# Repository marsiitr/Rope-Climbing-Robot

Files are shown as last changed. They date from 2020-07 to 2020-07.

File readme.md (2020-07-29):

<h1>Rope-Climbing-Robot</h1>
 <p align="justify">
Srishti 2020
</p>

## Abstract ##
<p align="justify">
This Rope climbing bot is used to climb ropes in an easy and efficient manner to reduce manual labour.Motorised rollers are used for climbing and a leadscrew is used for the gripping.
</p>
<p align="centre">
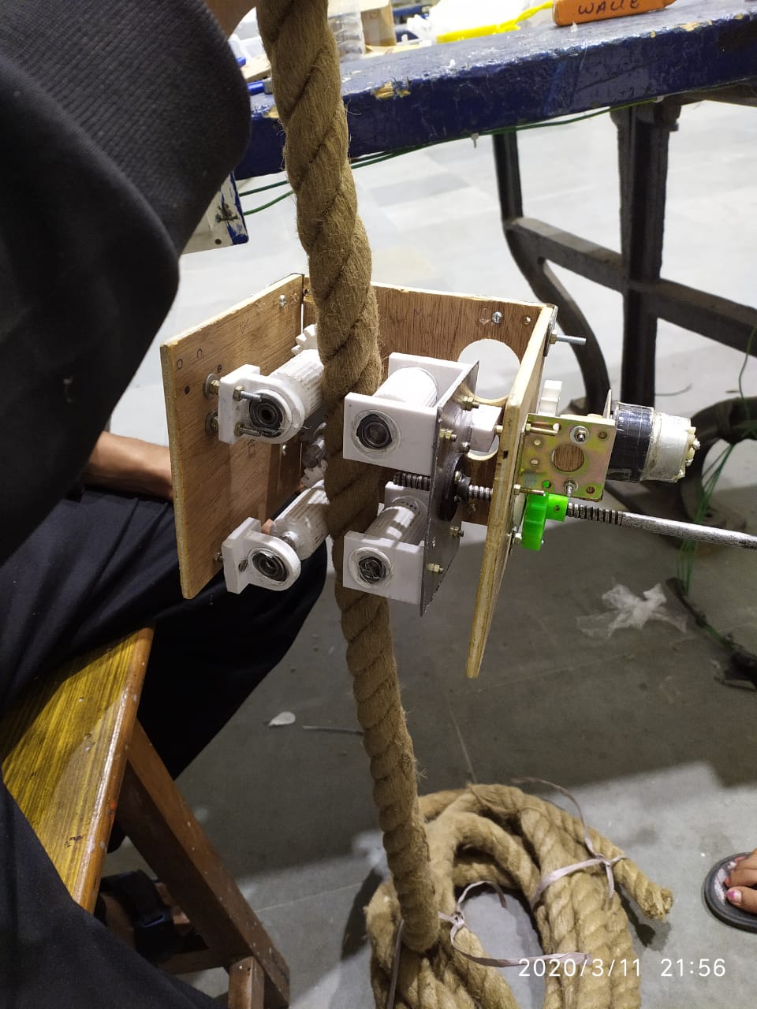
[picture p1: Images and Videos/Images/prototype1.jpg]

<!-- abstract-->
</p>

## Motivation ##
  <p align="justify">
People from various fields like mining , military , or other often come across situations where they can not get direct access to certain area say inside a cave in a mine .
There was a need of rope climbing robot which uses a single rope and can reach easily to any desired place in any terrain and most of the robots we come across uses double rope and are difficult to use. Also many day to day households work can be done easily with a rope climbing robot and thus we need a robot which can used in daily lives .     
</p>
<!-- motivation-->

## Mechanical aspect ##
<p align="justify">
In rope climbing robot two aspects are especially important grip on the rope and smoothness while movement . <br>
These two characteristics are important to carry a weight with a robot and easily maintain a overall stability of the robot . The design presented here for rope climmbing is a wheel based system since they are highly and easy to build.
</p>

#### Sliding roller ####
<p align="justify">
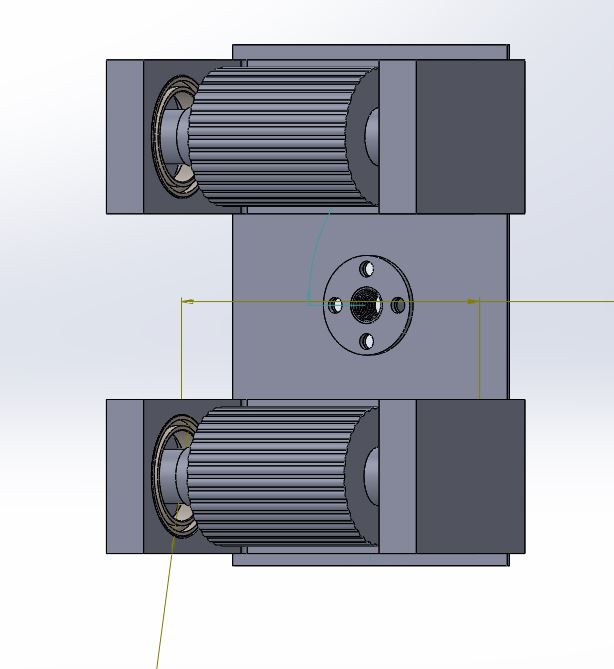
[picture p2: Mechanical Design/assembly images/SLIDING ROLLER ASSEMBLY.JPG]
<br>
This is a common and serves in both gripping mechanism and climbing mechanism . The assembly consists of two wheels attached to a rectangular metal sheet which is attached to the lead screw nut .<br>
The wheels are connected to the sheet with 3-D printed supports , bearings and shafts such that they are free to rotate about the shaft .
</p>

#### Encoder motor assembly ####
<p align="justify">
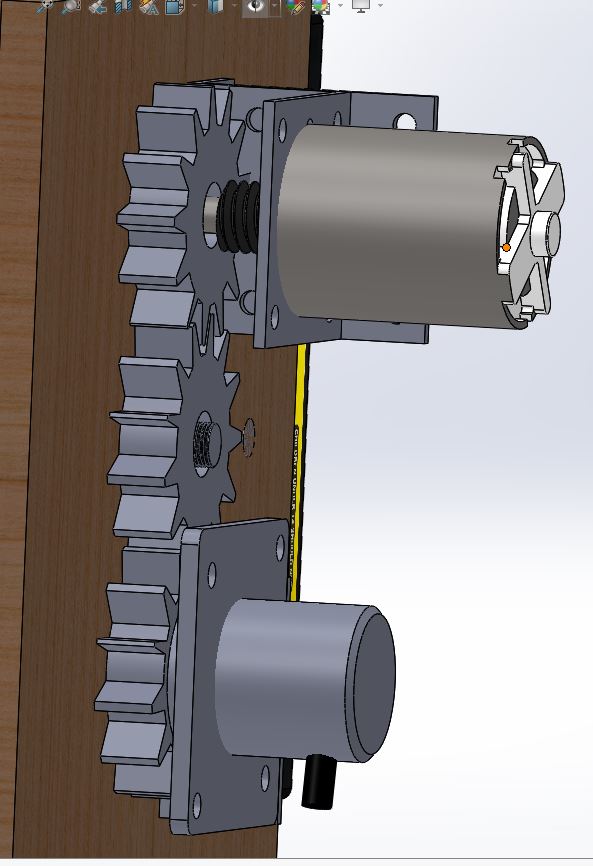
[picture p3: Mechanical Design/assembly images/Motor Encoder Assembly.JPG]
<br>
To grip the rope , sliding roller assembly has  to ascend on a lead screw , for that a spur gear is attached to the lead screw on the rear side . An encoder and motor are also attached sideways such that the lead screw attached to the spur gear simultaneously runs the spur gear attached to the encoder and the motor. <br>
For the working of the assembly , when the motor rotates , the spur gear rotates the lead screw which in turn rotates the encoder shaft through the trail of gears . The information of number of the rotations which the motor has to perform is already calculated and fitted into the encoder . Thus we can grip the rope.
</p>

#### Slider assembly ####
<p align="justify">
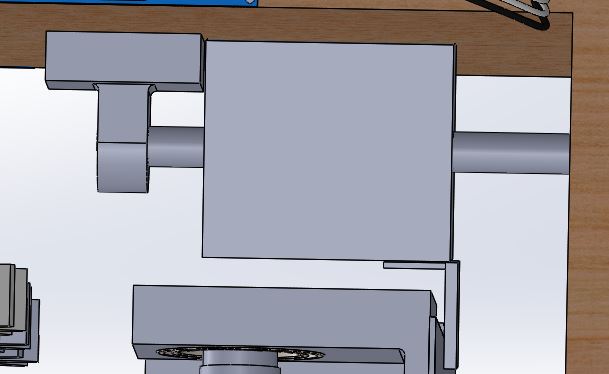
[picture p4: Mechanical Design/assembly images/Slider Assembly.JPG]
<br>
To prevent the sliding roller assembly to deviate from its path in a rotatory motion it is supported with a slider assembly. The slider is created with a shaft and a rectangular box which can slide on it . It is connected to "SRE" by a L hinge. <br>
The slider also creates a second support for the lead screw . Otherwise the lead screw will deviate from its position.
</p>

#### Motor wheel assembly ####
<p align="justify">
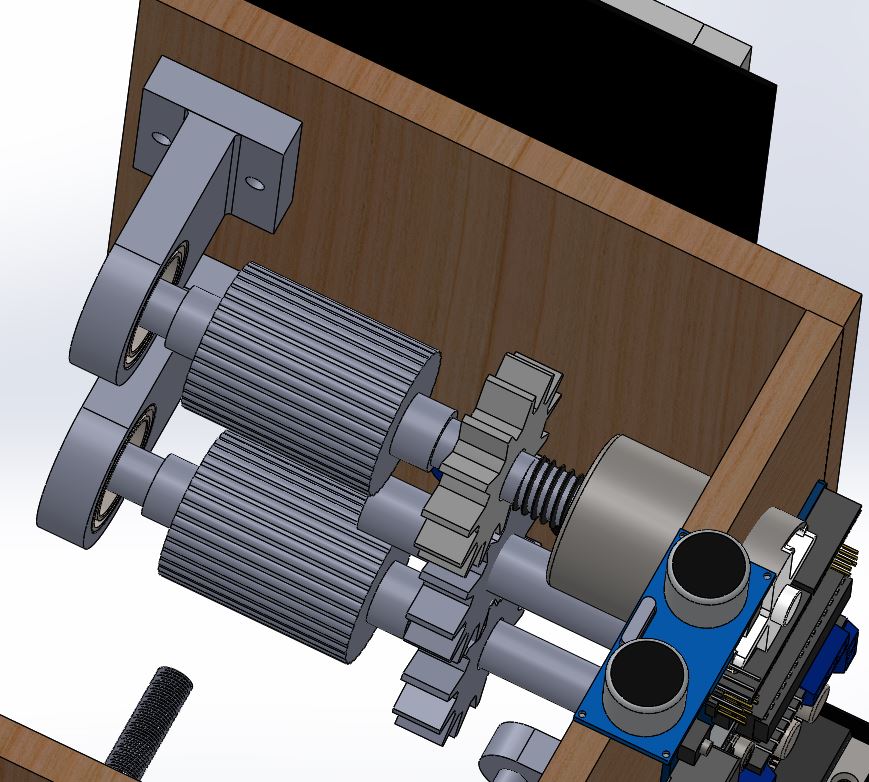
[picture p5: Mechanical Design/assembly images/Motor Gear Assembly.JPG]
<br>
After gripping the rope firmly, the bot has to climb the rope . The basic principal used along the rope is rolling. <br>
The design consists of a DC motor which is connected to three spur gear asssembly . The end gears are connected to each wheel . The design consists of two wheel pairs on either side of the rope. <br>
The wheels rolls on the surface of the rope which is powered by a DC motor (motor should provide high torque and power). In presence of sufficient friction between the wheels and the rope , the robot traverses the rope . The wheel should offer sufficient friction to support the robot in the vertical position . <br>
The other way to arrange the wheels is in a zig-zag pattern which increases the area of contact which in turn increases the friction.<br>
Let the radius of the wheel be r and θ is the angle of contact and h is the rope thickness. The surface area S in contact with the wheel is given as <br>
 <blockquote>S = (2πrhθ)/360</blockquote>
</p>

## Electronic aspect ##

- Electronic Components used
  
 1. Arduino Uno
 2. dc motors
 3. Ultrasonic distance sensors
 4. Encoder
 5. L298n motor controller
 6. Battery
 7. Connecting wires and jumpers
 
- Total two dc motors were used. One to grab the rope with the help of an encoder and the second for climbing the rope.</li>
- Two ultrasonic distance sensors were used to measure the distance of the bot from the floor and the top end of the rope.</li>
- dc motors were powered through Li-Po 12V dc battery.</li>

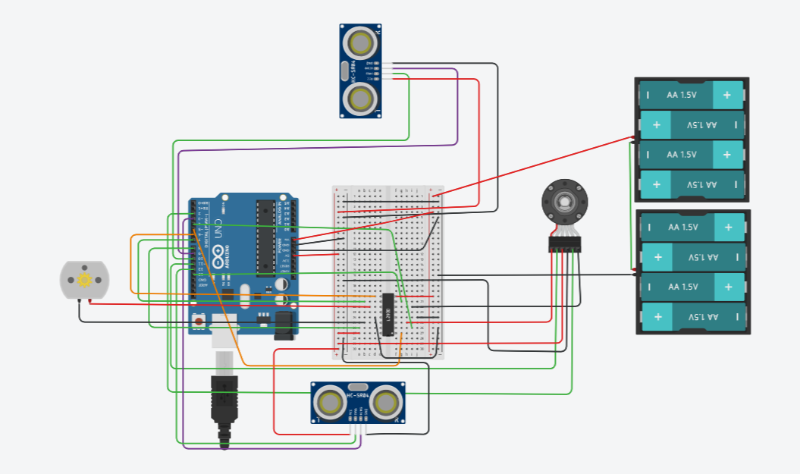
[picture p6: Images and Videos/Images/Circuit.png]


## Workflow ##

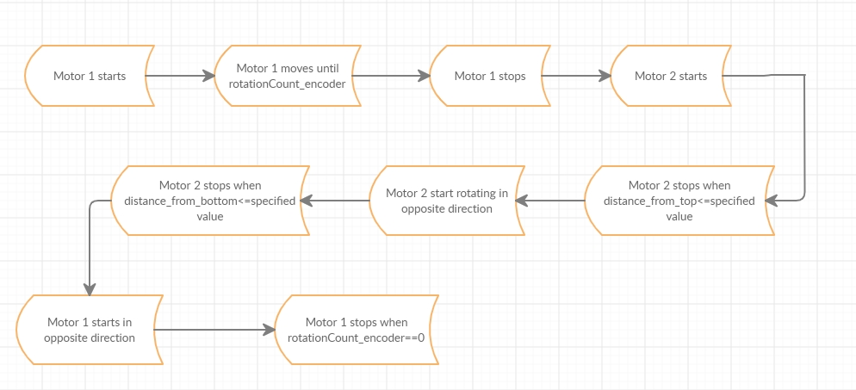
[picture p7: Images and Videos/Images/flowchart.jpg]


## Cost structure ##

<!-- cost structure-->

| materials|quantity|cost|
|:-----|:-----|:-----|
|Arduino UNO|1|425|
|Lipo battery|1|1100|
|Motor controller|1|160|
|Ultrasonic sensor|2|360|
|DC motor|2|300|
|Lead screw|1|600|
|Materials for body|1|1230|
|Manufacturing|1|600|
|*total*||4775|

## Applications ##

<p align="justify">
Robot is planned to serve the following tasks:
</p>

- It can be used to carry weights or to drop weights from some height.

- When equipped with camera, the robot can be used for surveillence.

- When equipped with cleaners, it can be used to clean glasses of windows or walls.

- Robot can be used to take pictures or to make videos from different heights.

<!-- apllications-->
## Limitations ##

1. The bot cannot climb horizontal ropes or ropes at some Angles.

2. The bot cannot traverse rope having some obstacles like knots or bend.

## Future improvements ##

1. The load carrying capacity can be improved by using stronger motors and parts.
2. Image detection software can be incorporated with the help of a camera , so that it can detect a rope on its own and climb it.
3. Modification in the design can be made so that it can measure its diameter of the rope without prefeding the data into the encoder.
4. Pneaumatics can be introduced in the the model to improve the gripping and climbing speed.

## Team Member ##

1. <a href="https://github.com/adityatidke">Aditya Tidke</a>
2. <a href="https://github.com/anu-cn">Anjali Rana</a>
3. <a href="https://github.com/parul253">Parul Chaudhary</a>
4. <a href="https://github.com/guddu-gupta">Tanisha Gupta</a>
5. <a href="https://github.com/vanshgoyal">Vansh Goyal</a>
6. <a href="https://github.com/vinusebastian265">Vinu Sebastian</a>

## Mentor ##

1. <a href="https://github.com/avdeshranwa">Avdesh Ranwa</a>
2. Gautam Jha

## Refrences ##

https://www.arrow.com/en/research-and-events/articles/ultrasonic-sensors-how-they-work-and-how-to-use-them-with-arduino <br>
https://www.thomasnet.com/articles/machinery-tools-supplies/pneumatic-actuators/<br>
https://www.instructables.com/circuits/arduino/projects/<br>
https://grabcad.com/

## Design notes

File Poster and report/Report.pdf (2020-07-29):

# Climbing

# Rope

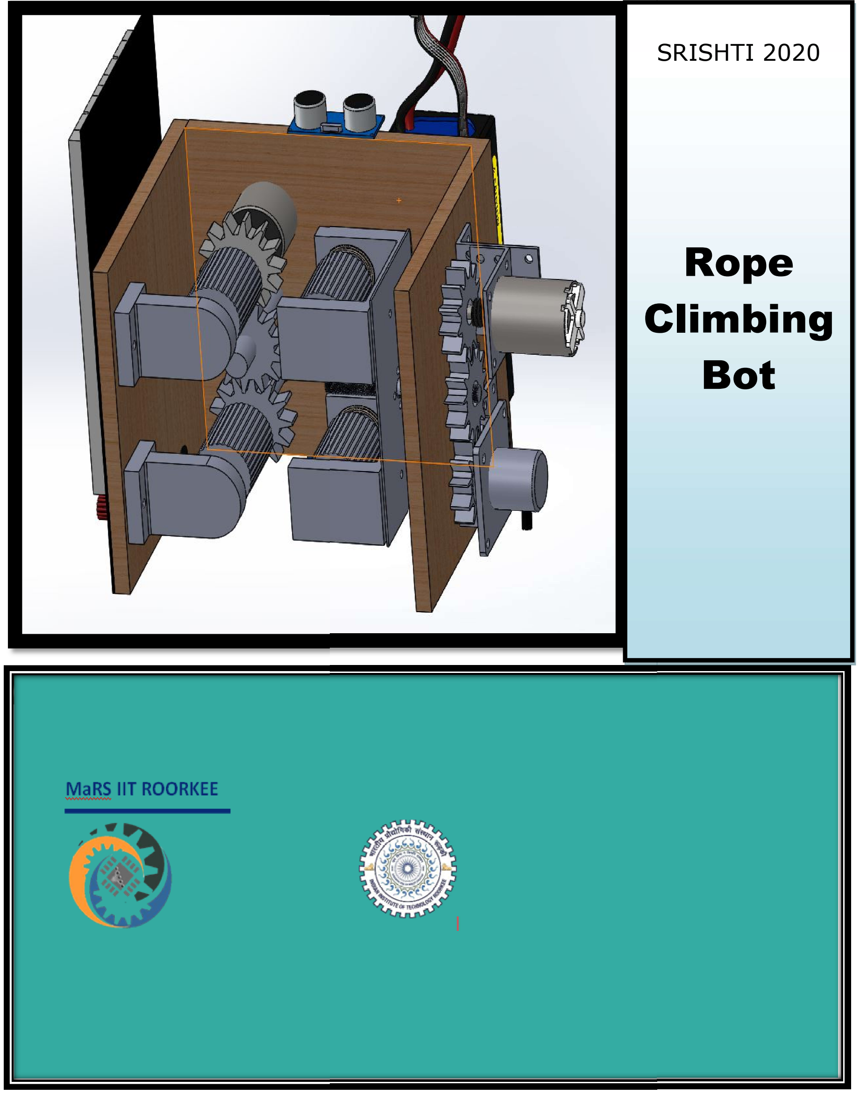
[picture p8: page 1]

SRISHTI 2020

# Climbing Bot

2

## Team Members

Aditya Tidke
Anjali Rana
Parul Chaudhary
Tanisha Gupta
Vansh Goyal
Vinu Sebastian

## Team Mentors

Avdesh Ranwa
Gautam Jha

# Rope-Climbing-Robot

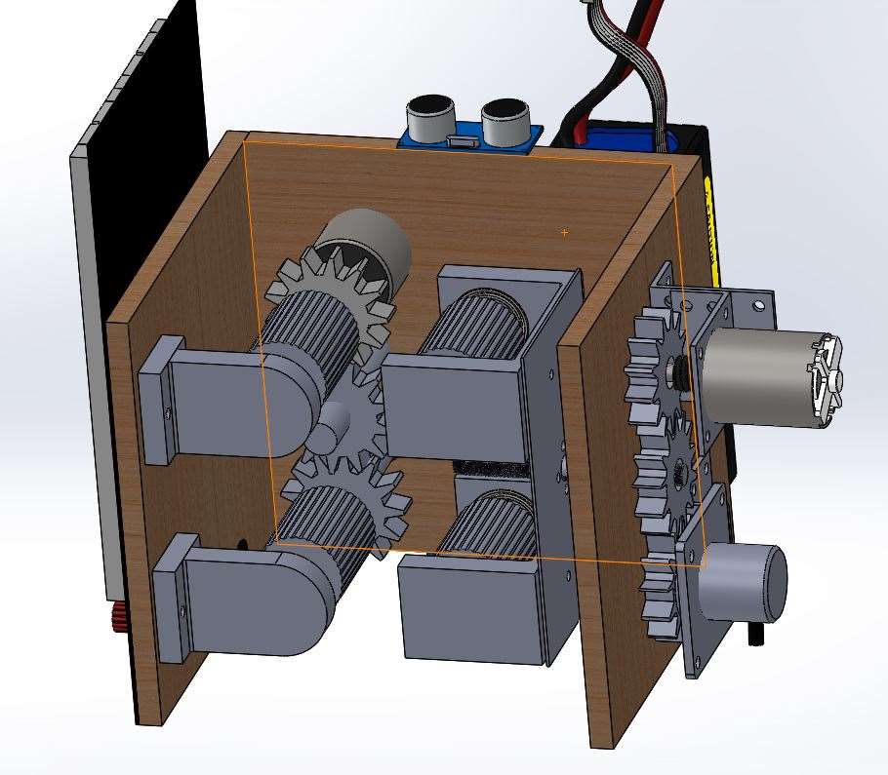
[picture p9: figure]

## Abstract

This Rope climbing bot is used to climb ropes in an easy and efficient manner to reduce manual labour. Motorised rollers are used for climbing and a lead screw is used for the gripping.

4

## Motivation

People from various fields like mining, military, or other often come across situations where they cannot get direct access to certain area say inside a cave in a mine. There was a need of rope climbing robot which uses a single rope and can reach easily to any desired place in any terrain and most of the robots we come across uses double rope and are difficult to use. Also many day to day households work can be done easily with a rope climbing robot and thus we need a robot which can used in daily lives.

## Mechanical aspect

In rope climbing robot two aspects are especially important grip on the rope and smoothness while movement. These two characteristics are important to carry a weight with a robot and easily maintain a overall stability of the robot. The design presented here for rope climbing is a wheel based system since they are highly and easy to build.

Sliding roller

This is a common and serves in both gripping mechanism and climbing mechanism. The assembly consists of two wheels attached to a rectangular metal sheet which is attached to the lead screw nut. The wheels are connected to the sheet with 3-D printed supports, bearings and shafts such that they are free to rotate about the shaft.

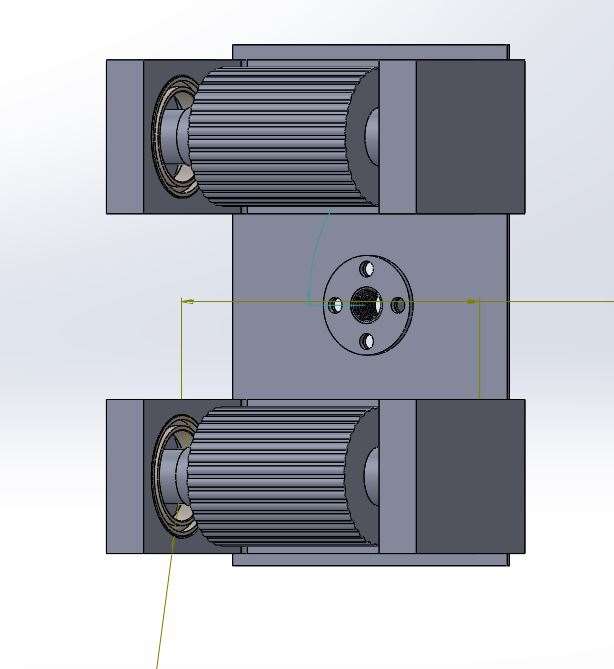
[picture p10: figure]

Sliding roller assembly
Encoder motor assembly

To grip the rope, sliding roller assembly has to ascend on a lead screw, for that a spur gear is attached to the lead screw on the rear side. An encoder and motor are also attached sideways such that the lead screw attached to the spur gear simultaneously runs the spur gear attached to the encoder and the motor. For the working of the assembly, when the motor rotates, the spur gear rotates the lead screw which in turn rotates the encoder shaft through the trail of gears. The information of number of the rotations which the motor has to perform is already calculated and fitted into the encoder. Thus we can grip the rope.

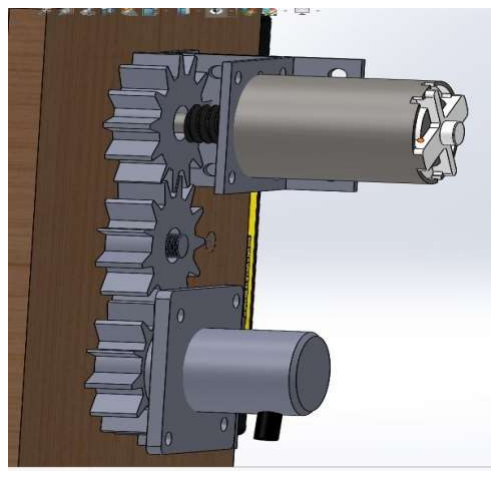
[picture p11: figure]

Encoder motor assembly

Slider assembly

To prevent the sliding roller assembly to deviate from its path in a rotating motion it is supported with a slider assembly. The slider is created with a shaft and a rectangular box which can slide on it. It is connected to sliding roller assembly by a L hinge. The slider also creates a second support for the lead screw. Otherwise the lead screw will deviate from its position.

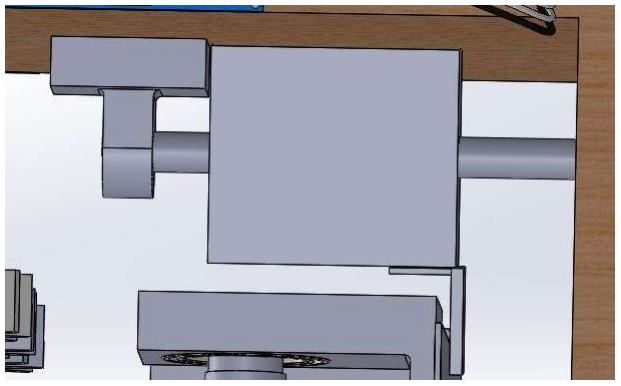
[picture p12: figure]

Sliding assembly
Motor wheel assembly

After gripping the rope firmly, the bot has to climb the rope. The basic principal used along the rope is rolling. The design consists of a DC motor which is connected to three spur gear assembly. The end gears are connected to each wheel. The design consists of two wheel pairs on either side of the rope. The wheels roll on the surface of the rope which is powered by a DC motor (motor should provide high torque and power). In presence of sufficient friction between the wheels and the rope, the robot traverses the rope. The wheel should offer sufficient friction to support the robot in the vertical position.

The other way to arrange the wheels is in a zigzag pattern which increases the
area | of | contact | which | in | turn | increases | the | friction.
Let the radius of the wheel be r and θ is the angle of contact and h is the rope thickness. The surface area S in contact with the wheel is given as

S = (2πrhθ)/360

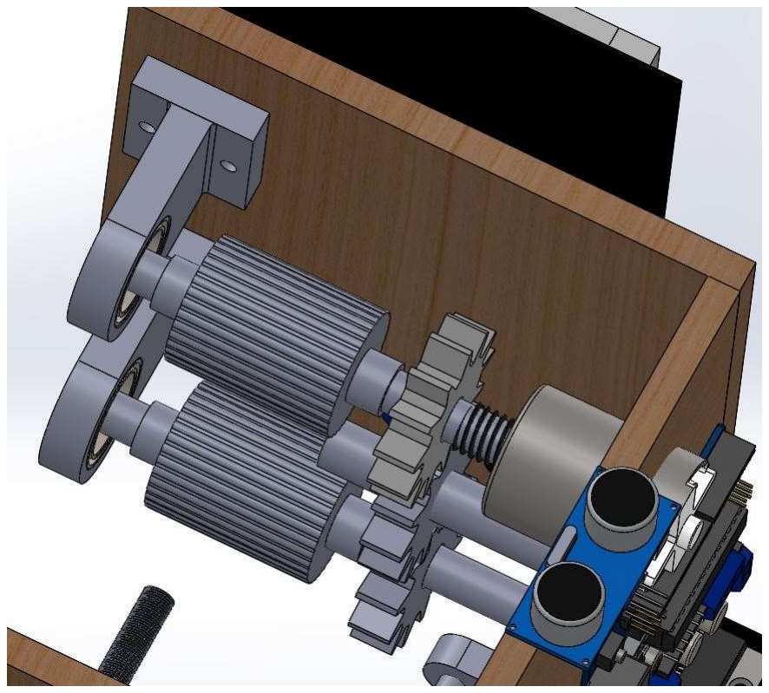
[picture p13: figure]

Motor wheel assembly

Electronic aspect Electronic Components used

### 1. Arduino Uno

### 2. dc motors

### 3. Ultrasonic distance sensors

### 4. Encoder

### 5. L298n motor controller

### 6. Battery

### 7. Connecting wires and jumpers

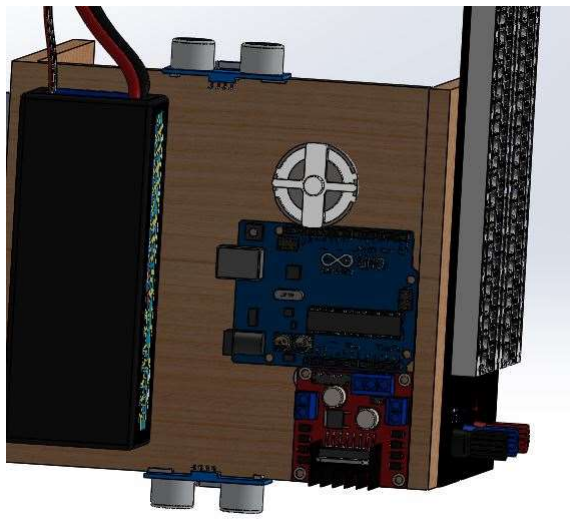
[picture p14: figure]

- Total two dc motors were used. One to grab the rope with the help of an encoder and the second for climbing the rope. Two ultrasonic distance sensors were used to measure the distance of the bot

from the floor and the top end of the rope.

- dc motors were powered through Li

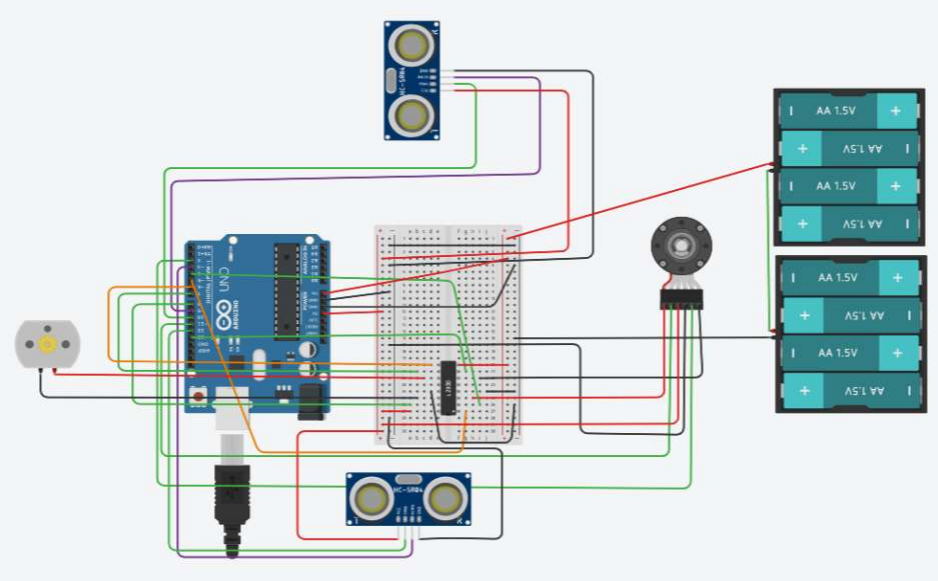
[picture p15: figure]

## Cost structure

materials

Arduino UNO

Lipo battery

-Po 12V dc

quantity

1

1

cost

425

1100

10

materials | quantity | cost
Motor controller | 1 | 160
Ultrasonic sensor | 2 | 360
DC motor | 2 | 300
Lead screw | 1 | 600
Materials for body | 1 | 1230
Manufacturing | 1 | 600
Total | | 4775

## Applications

Robot is planned to serve the following tasks:

- It can be used to carry weights or to drop weights from some height.
- When equipped with camera, the robot can be used for surveillance.

11

- When equipped with cleaners, it can be used to clean glasses of windows or walls.
- Robot can be used to take pictures or to make videos from different heights.

## Limitations

- The robot cannot climb horizontal ropes or ropes at some angles.
- The robot cannot rope having some obstacles like knots or bend.

## Future improvements

1. The load carrying capacity can be improved by using stronger motors and parts.

### 2. Image detection software will be incorporated with the help of a camera, so that it

can detect a rope on its own and climbs it.

### 3. Modification in the design will be made so that it can measure its diameter of the

rope without prior feeding of the data into the encoder.

### 4. Pneumatics can be introduced in the model to improve the gripping and climbing

speed.

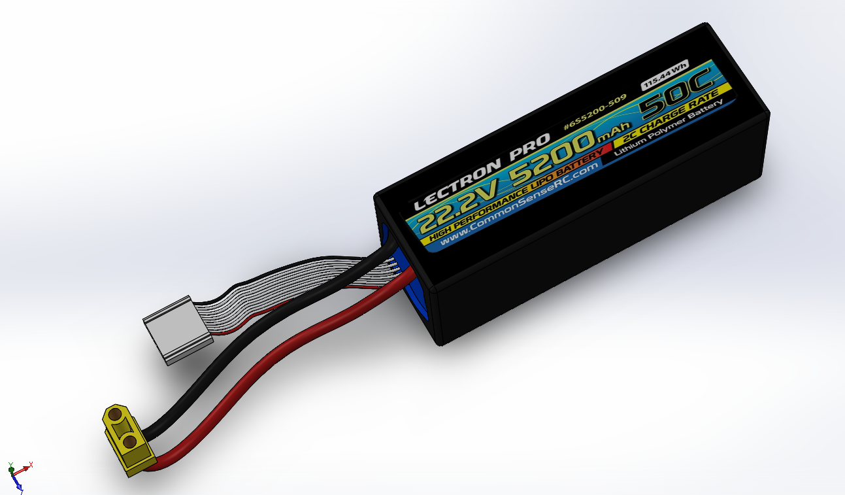
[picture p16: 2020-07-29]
Mechanical Design/BATERIAS/LIPO BATERRY.png

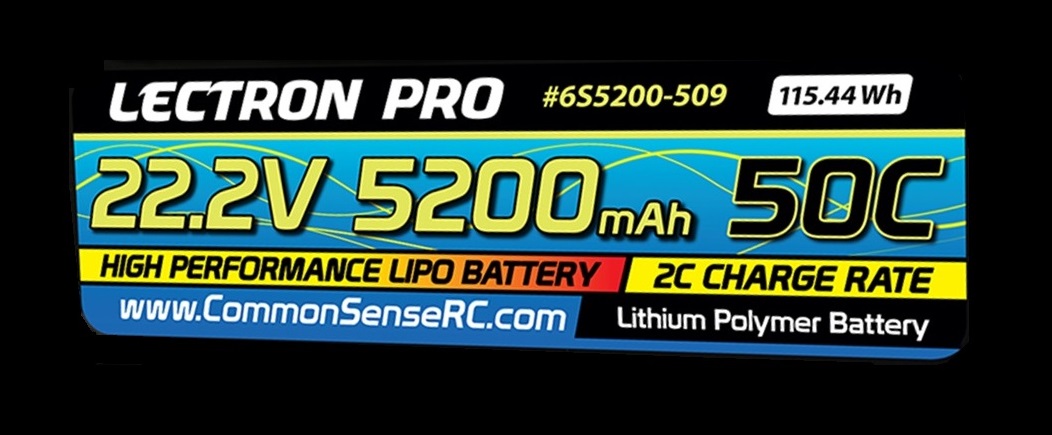
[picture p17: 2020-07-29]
Mechanical Design/BATERIAS/LECTRO PRO 22,2V 5200MAH.jpg

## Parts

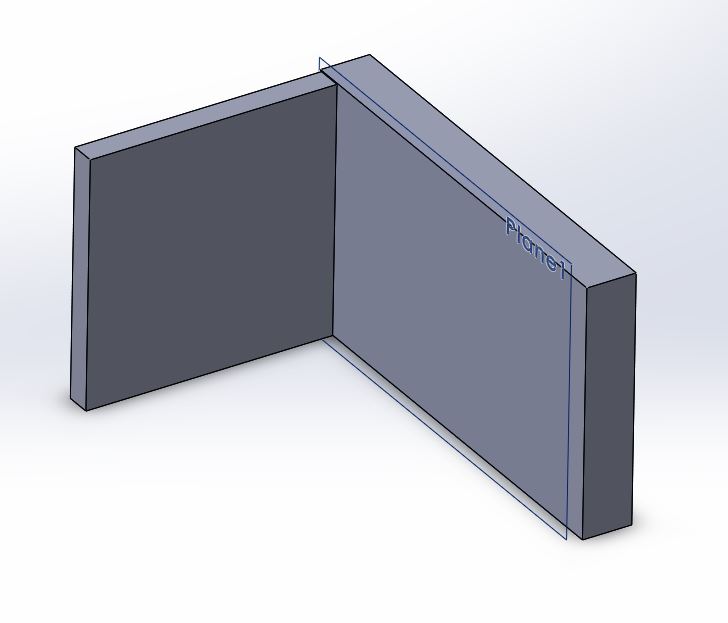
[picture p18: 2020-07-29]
Mechanical Design/Parts images/Image RCB Connector L hinge.JPG

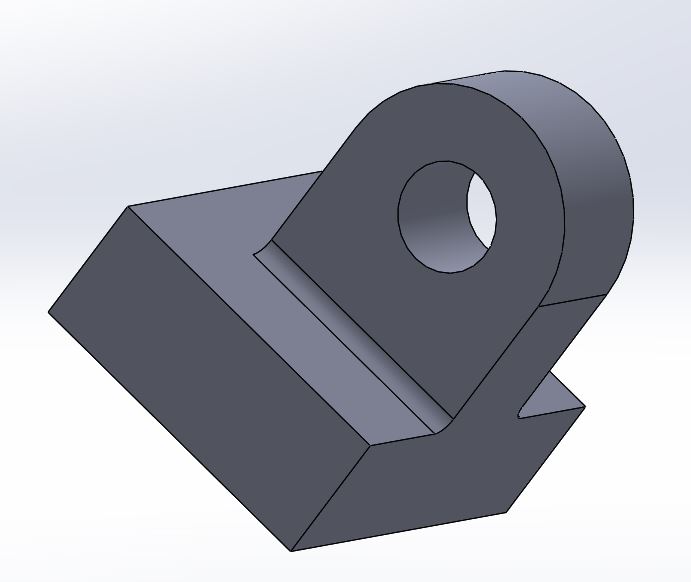
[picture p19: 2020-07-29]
Mechanical Design/Parts images/Image RCB Slider Bearing block.JPG

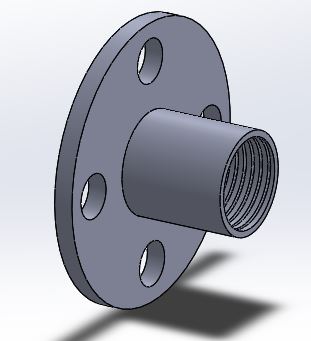
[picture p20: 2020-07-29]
Mechanical Design/Parts images/Image RCB Lead screw (Nut).JPG

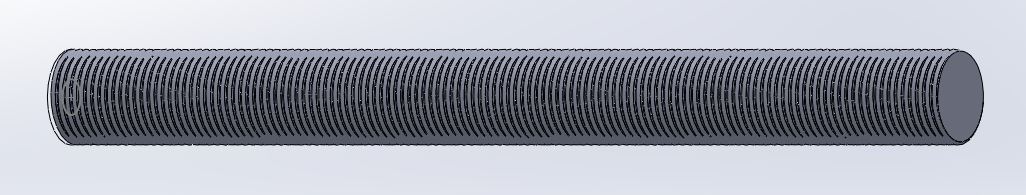
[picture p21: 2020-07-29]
Mechanical Design/Parts images/ImageRCB Lead SCREW(Shaft).JPG

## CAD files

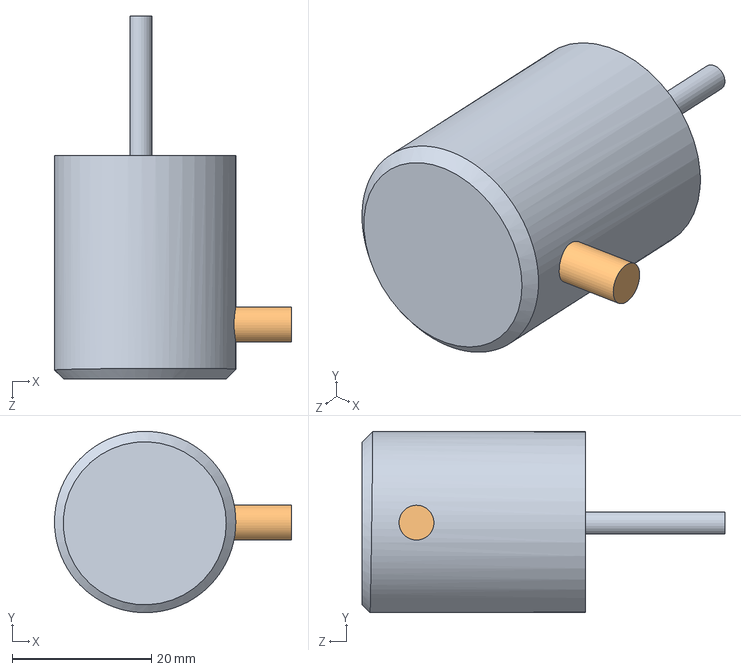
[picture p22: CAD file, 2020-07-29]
Mechanical Design/encoder/encoder f.SLDASM
34.0 x 26.0 x 52.0 mm

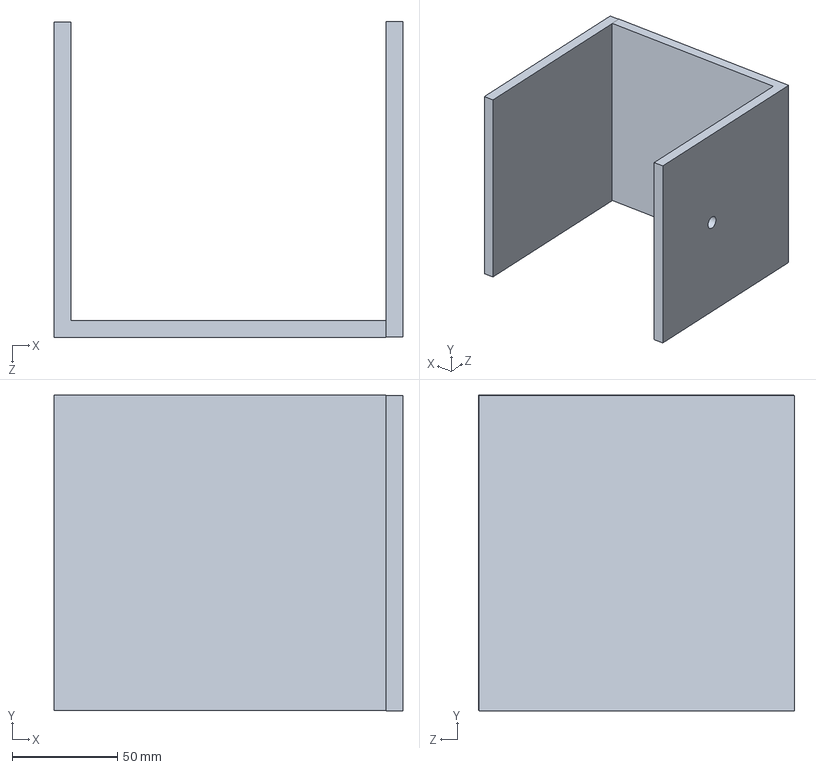
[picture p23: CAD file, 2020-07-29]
Mechanical Design/RCB Main Bot Frame.SLDPRT
166.0 x 150.2 x 150.1 mm

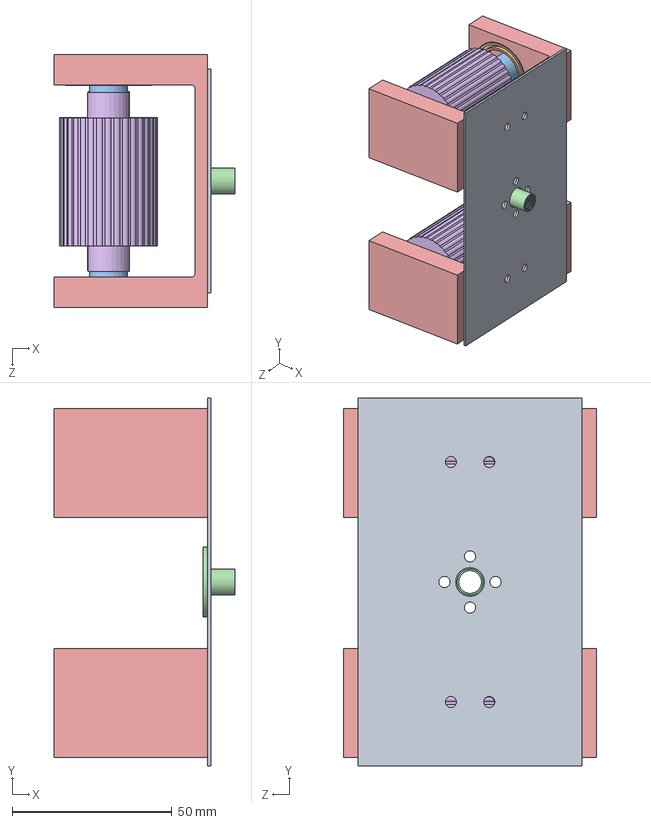
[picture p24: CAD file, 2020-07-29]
Mechanical Design/RCB Sliding Roller Assembly.SLDASM
56.5 x 115.0 x 79.0 mm
RCB Roller Hoding Plate
instrument ball bearing_68_am x 4
RCB Shaft(short) SR Assembly x 2
RCB Lead screw (Nut)
RCB Rope Wheel Holder x 2
RCB Rope Wheel x 2

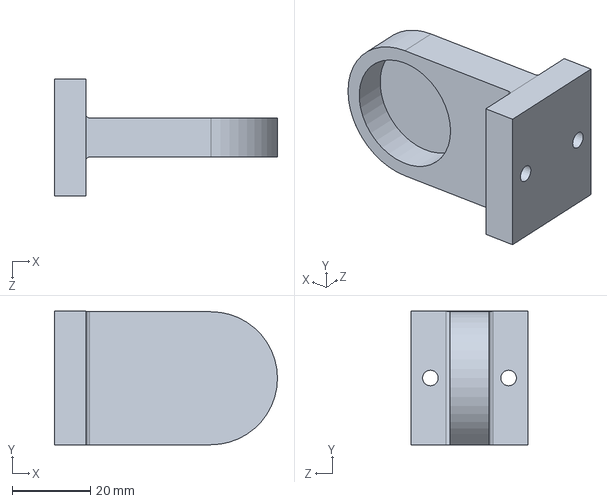
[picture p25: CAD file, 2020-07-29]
Mechanical Design/RCB Bearing Block(Motor Assembly).SLDPRT
57.0 x 34.1 x 30.0 mm

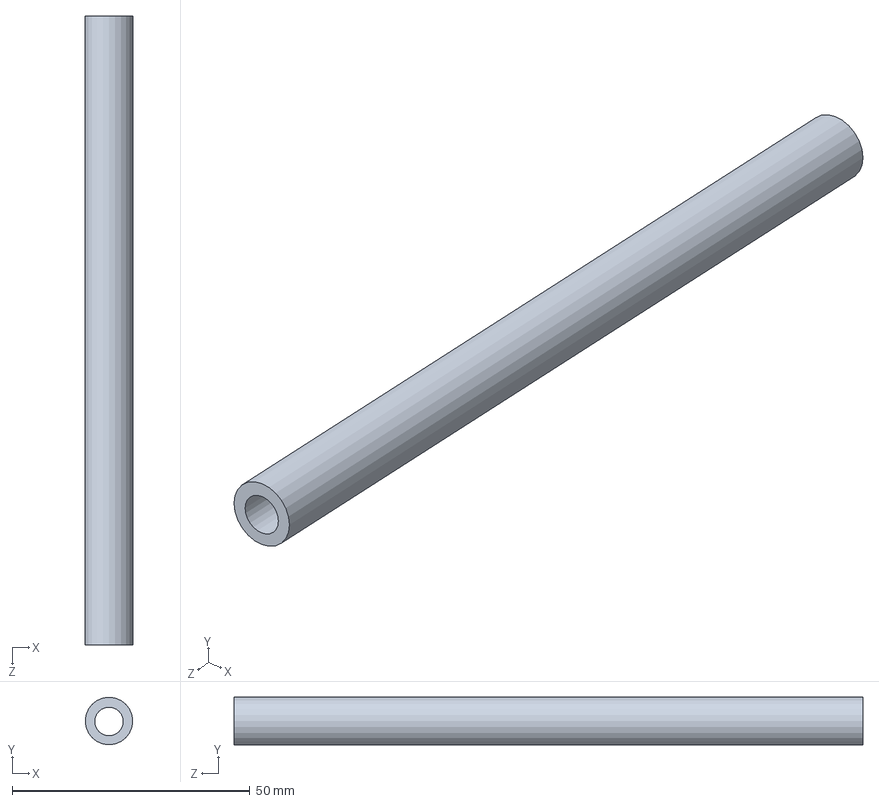
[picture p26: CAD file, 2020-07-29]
Mechanical Design/RCB Shaft(Long) Motor Assembly.SLDPRT
10.0 x 10.0 x 132.4 mm

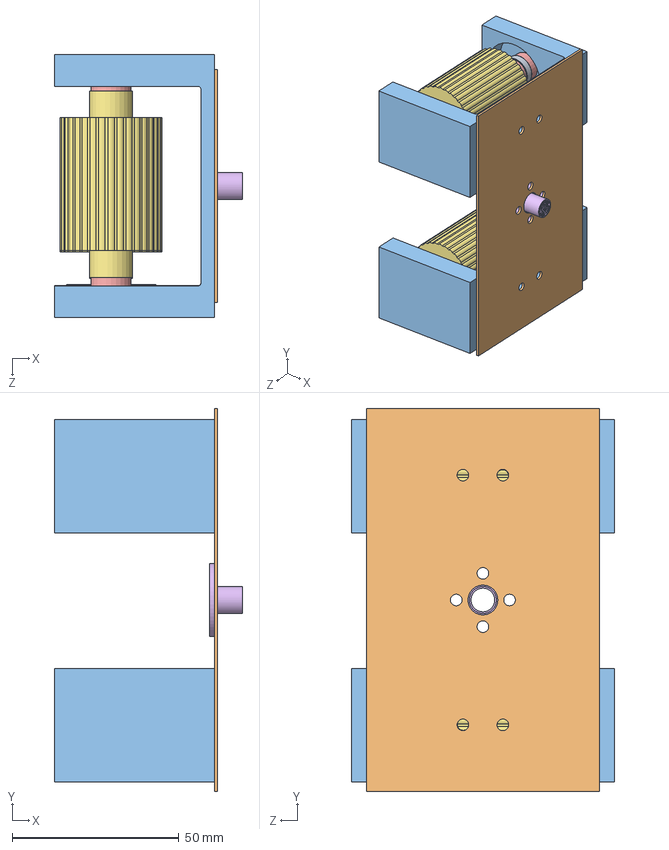
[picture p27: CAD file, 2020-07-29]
Mechanical Design/moving assem.SLDASM
56.5 x 115.0 x 79.1 mm
connecting plate
wheel block x 2
instrument ball bearing_68_am x 4
rb shaft short x 2
nut lead screw
new wheel x 2

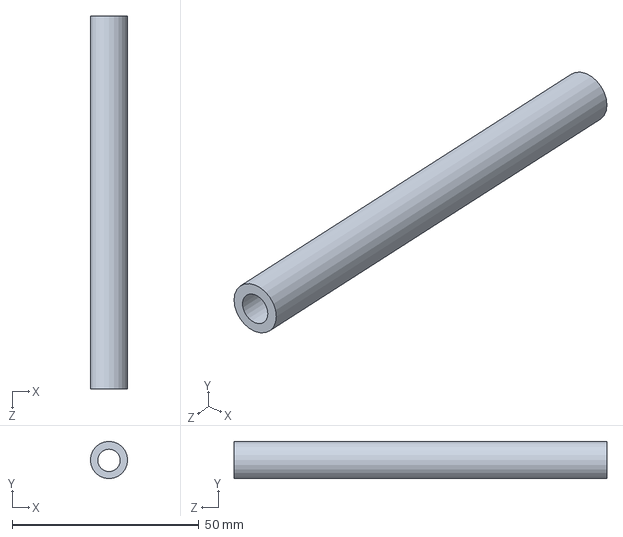
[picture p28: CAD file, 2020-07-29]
Mechanical Design/RCB Shaft(Medium) Motor Assembly.SLDPRT
10.0 x 10.0 x 100.0 mm

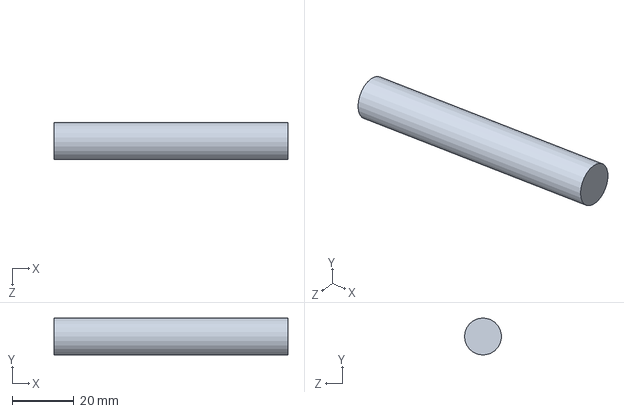
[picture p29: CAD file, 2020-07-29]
Mechanical Design/RCB Shaft(short) SR Assembly.SLDPRT
76.0 x 12.0 x 12.0 mm

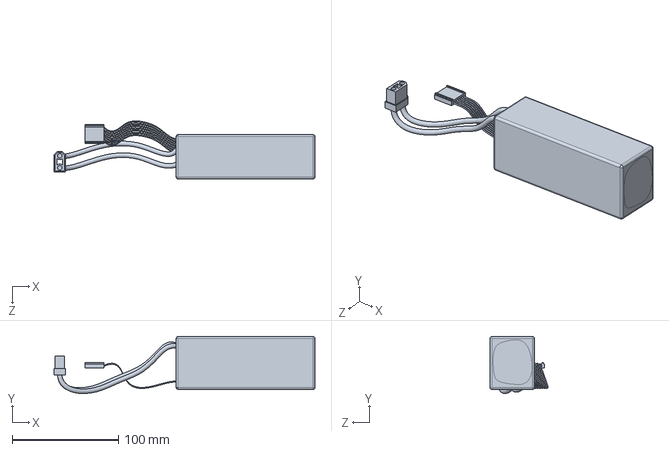
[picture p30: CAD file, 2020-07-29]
Mechanical Design/BATERIAS/BATERIA.SLDPRT
246.2 x 53.8 x 54.8 mm

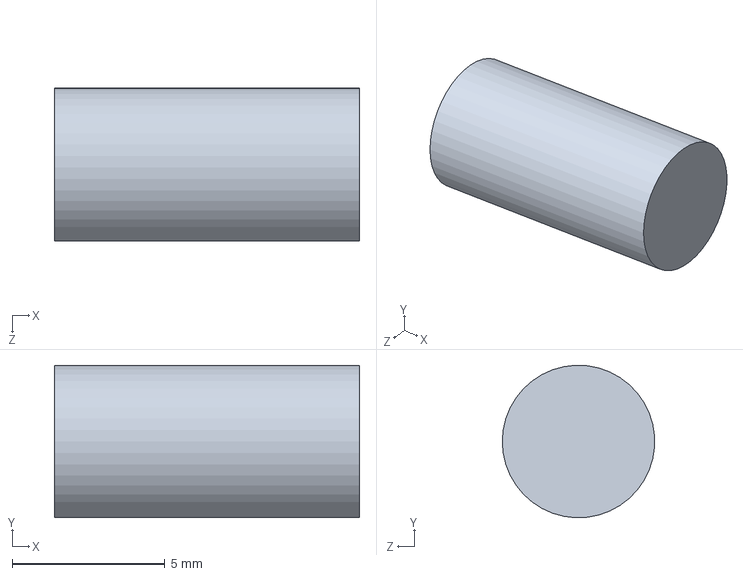
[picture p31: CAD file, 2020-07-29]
Mechanical Design/encoder/Part2.SLDPRT
10.0 x 5.00 x 5.00 mm

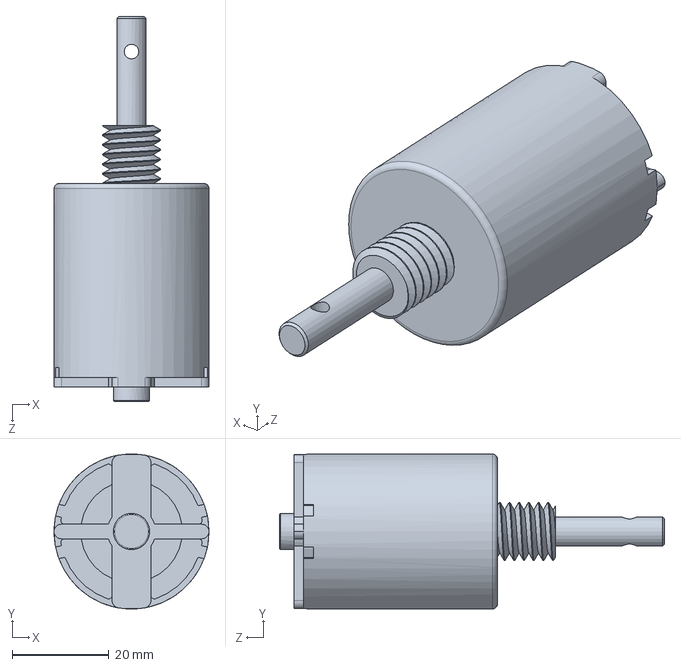
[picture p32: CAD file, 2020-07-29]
Mechanical Design/Motor DC.SLDPRT
32.0 x 32.0 x 79.5 mm

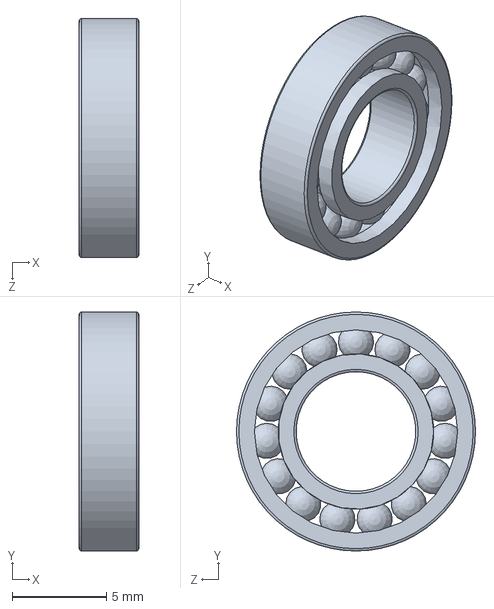
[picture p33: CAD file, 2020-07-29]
Mechanical Design/RCB Bearings/instrument ball bearing_68_am2.SLDPRT
3.17 x 12.7 x 12.7 mm

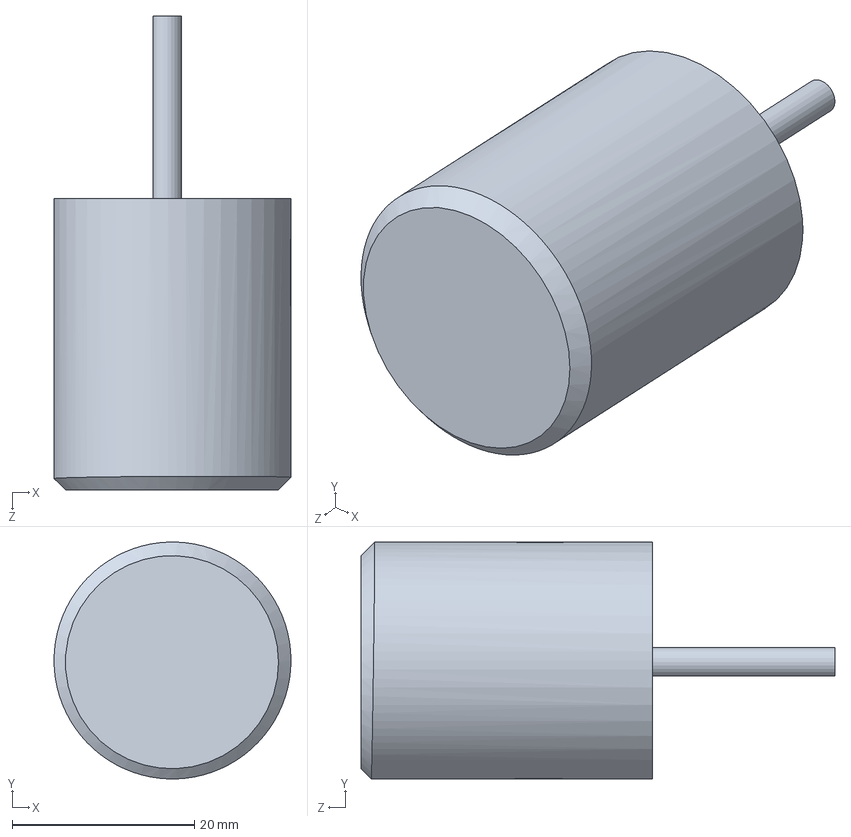
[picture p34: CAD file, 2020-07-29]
Mechanical Design/encoder/Part1.SLDPRT
26.0 x 26.0 x 52.0 mm

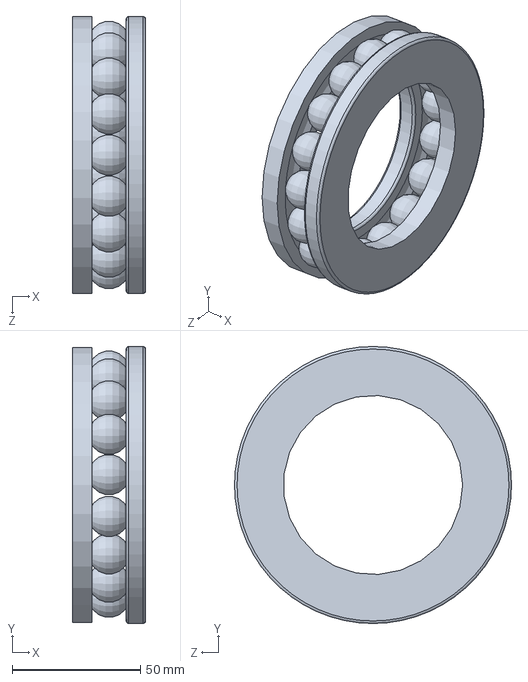
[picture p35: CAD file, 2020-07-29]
Mechanical Design/RCB Bearings/thrust ball bearing4_68_am.sldprt
28.6 x 108.0 x 108.0 mm

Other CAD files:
Mechanical Design/RCB Connector L hinge.SLDPRT
Mechanical Design/RCB Bearings/instrument ball bearing_68_am.sldprt
Mechanical Design/RCB Bearings/thrust ball bearing3_68_am.sldprt
Mechanical Design/RCB Spur Gear.SLDPRT
Mechanical Design/RCB Bearings/radial ball bearing_68_am.sldprt
Mechanical Design/RCB Bearings/thrust ball bearing2_68_am.sldprt
Mechanical Design/RCB Bearings/thrust ball bearing_68_am.sldprt
Mechanical Design/RCB Dc Motor Hinge.SLDPRT
Mechanical Design/RCB Encoder Coupling.SLDPRT
Mechanical Design/RCB Lead SCREW(Shaft).SLDPRT
Mechanical Design/RCB Lead screw (Nut).SLDPRT
Mechanical Design/RCB Roller Hoding Plate .SLDPRT
Mechanical Design/RCB Rope Wheel Holder.SLDPRT
Mechanical Design/RCB Rope Wheel.SLDPRT
Mechanical Design/RCB SLIDER.SLDPRT
Mechanical Design/RCB Shaft (Slider).SLDPRT
Mechanical Design/RCB Slider Bearing block.SLDPRT
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

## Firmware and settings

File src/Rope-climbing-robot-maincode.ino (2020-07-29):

#define encoderPinA 2
#define encoderPinB 11

int rotationCount_encoder=0;//no of rotation of encoder
int total_rotation=2000;//total encoder count to grip the rope

//motor 1 is used to grip the rope
//motor 2 is used to climb up and down
int motor1_pwm=5;
int motor2_pwm=6;
int SPEED_motor1=200;
int SPEED_motor2=50;
int motor1Pin1=4;
int motor1Pin2= 13;
int motor2Pin1=7;
int motor2Pin2= 8;

//ultrasonic1 is to measure distance from the bot to the above
//ultrasonic2 is to measure distance from the bot to the floor
int ultrasonic1_echo=9;
int ultrasonic1_trig=10;
int ultrasonic2_echo= 3;
int ultrasonic2_trig=12;
long distance_from_top=0;
long distance_from_bottom=0;

int n=0;/*it is a variable to check that the bot does not go up 
again, after comming to a certain distance*/


void setup() 
{
  Serial.begin(9600);
  pinMode(motor1_pwm,OUTPUT);
  pinMode(motor2_pwm,OUTPUT);
  pinMode(motor1Pin1,OUTPUT);
  pinMode(motor1Pin2,OUTPUT);
  pinMode(motor2Pin1,OUTPUT);
  pinMode(motor2Pin2,OUTPUT);
  pinMode(encoderPinA, INPUT_PULLUP);
  pinMode(encoderPinB, INPUT_PULLUP);
  pinMode(ultrasonic1_echo,INPUT);
  pinMode(ultrasonic1_trig,OUTPUT);
  pinMode(ultrasonic2_echo,INPUT);
  pinMode(ultrasonic2_trig,OUTPUT);
  
  attachInterrupt(0, doEncoder, CHANGE);
}
void doEncoder()
{
  if(digitalRead(encoderPinA)!=digitalRead(encoderPinB))
  {
  rotationCount_encoder++;
  }
  else
  {
  rotationCount_encoder--;
  }
}
long ultrasonic1()
{
  long duration,distance;
 digitalWrite(ultrasonic1_trig,LOW);
  digitalWrite(ultrasonic1_trig,HIGH);
  delayMicroseconds(1000);
  digitalWrite(ultrasonic1_trig,LOW);
  duration=pulseIn(ultrasonic1_echo,HIGH);
  distance=(duration/2)*0.034;
  return distance;
}
long ultrasonic2()
{
  long duration,distance;
 digitalWrite(ultrasonic2_trig,LOW);
  digitalWrite(ultrasonic2_trig,HIGH);
  delayMicroseconds(1000);
  digitalWrite(ultrasonic2_trig,LOW);
  duration=pulseIn(ultrasonic2_echo,HIGH);
  distance=(duration/2)*0.034;
  return distance;
}


void loop() 
{
  
  if(rotationCount_encoder<total_rotation)//to grip the rope
  {
    analogWrite(motor1_pwm,SPEED_motor1);
	digitalWrite(motor1Pin1,LOW);
 	digitalWrite(motor1Pin2,HIGH);
  }
  else
  {
    analogWrite(motor1_pwm,0);
    digitalWrite(motor1Pin1,LOW);
    digitalWrite(motor1Pin2,LOW);
  }
  
  distance_from_top=ultrasonic1();
  distance_from_bottom=ultrasonic2();
  if(distance_from_top>100&&rotationCount_encoder>=total_rotation&&n%2==0)
  {
    analogWrite(motor2_pwm,SPEED_motor2);
    digitalWrite(motor2Pin1,LOW);
    digitalWrite(motor2Pin2,HIGH);
  }
  
  if(distance_from_top<=100&&rotationCount_encoder>=total_rotation)
  {
    analogWrite(motor2_pwm,SPEED_motor2);
    digitalWrite(motor2Pin1,HIGH);
    digitalWrite(motor2Pin2,LOW); 
    n=1;
   }
   
  if(distance_from_top>100&&n%2!=0)
  {
    analogWrite(motor2_pwm,SPEED_motor2);
    digitalWrite(motor2Pin1,HIGH);
    digitalWrite(motor2Pin2,LOW);
       if(distance_from_bottom<=30)
       {
         analogWrite(motor2_pwm,0);
         delay(5000);
         if(rotationCount_encoder>=0)//to remove the grip after coming down
          {
            analogWrite(motor1_pwm,SPEED_motor1);
            digitalWrite(motor1Pin1,HIGH);
            digitalWrite(motor1Pin2,LOW);
          }
         else
          {
           analogWrite(motor1_pwm,0);
          }
       }
  }

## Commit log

2020-07-27 cad files
    [2 bearing block.STL, Arduino UNO.SLDPRT, BATERIA.SLDPRT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]
2020-07-27 Flow Chart
2020-07-29 Mechanical Design
    [Arduino UNO.SLDPRT, BATERIA.SLDPRT, L298N Motor Driver.SLDPRT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]
